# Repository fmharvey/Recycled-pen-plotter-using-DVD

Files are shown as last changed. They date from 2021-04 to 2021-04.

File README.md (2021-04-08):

# Recycled-pen-plotter-using-DVD
A recycled pen plotter using stepmotors from recycled DVD, a servo motor and a suite of hardware/softwares from the OpenSource community : Arduino, GRBL-Servo, UniversalGCodeSender ,  J Tech Photonics Inkscape Laser Plug-In , LinuxMint, EasyDriver pilot. What's my contribution - for now to have found all the bits to make it works as of 2021, an original design for the pencil holder/plater and some nice documentation in french/english as it is intented to be used as an activity in Quebec schools.

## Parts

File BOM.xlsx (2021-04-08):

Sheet: BOM
Composantes/kit
 |  | 8
Ref Schéma | Qte/1 | QteTot | Description | Provenance | Coût | Lien
 | 1 | 8 | Arduino UNO | magasin techno
 | 1 | 8 | Câble USB type B | magasin techno
 | 1 | 8 | ProtoBoard présoudé pour EasyDriver | magasin techno
 | 2 | 16 | EasyDriver | achat-financé C4
 | 1 | 8 | Alimentation externe 9V conn barrel 2.2mmID x 5.2 mm
 | 5 | 40 | Broches mâles cassables 0.1'' 2 pos
 | 1 | 8 | Broches mâles cassables 0.1'' 4 pos
 | 1 | 8 | Broches mâles cassables 0.1'' 3 pos
 | 10 | 80 | Brôche femelle 0.1'' 2 pos
 | 2 | 16 | Brôche femelle 0.1'' 4 pos
 | 2 | 16 | Brôche femelle 0.1'' 3 pos
 | 6 | 48 | Spacer Nylon 6mm haut X 6mm OD X 3.5mmID-pour stack easyr driver+arduino | magasin techno
 | 6 | 48 | Écrous 4/40 - pour stack EasyDriver+arduino | magasin techno
 | 6 | 48 | Vis nylon 4/40 -pour stack Easy Driver+arduino | magasin techno
 | 2 | 16 | Harnais 4 fils pour stepmoteur-Terminaison jumper mâle
 | 17 | 136 | Fil jumper mâle-mâle-easyr driver à arduino | magasin techno
 | 1 | 8 | Ordinateur récupéré | RécuperAction
 | 2 | 16 | Lecteur DVD | RécuperAction/C4
 | 2 | 16 | Boîtier lecteur DVD pré-troué (Seront troués après que les participants les auront démonté) | RécuperAction/C4
 | 2 | 16 | Équerres
 | 8 | 64 | Spacer imprimé 3D pour tenir les plateau | imprimé
 | 4 | 32 | Vis 1/4 -20 - pour les équerres
 | 4 | 32 | Écrous 1/4 -20 pour les équerres
 |  | 0
 | 4 | 32 | Ressorts compression plateau OD 7mm X ID 6mm X 20 mm long | magasin techno-récup
 | 4 | 32 | Vis M2.5 X20mm | Récupéré Axion
 | 4 | 32 | Écrou carré M2.5 | Récupéré Axion
 | 6 | 48 | TyRap réutilisable-pour tenir les plateaux
 | 2 | 16 | Plateau imprimé 3D - support tête | imprimé
 | 1 | 8 | Plateau à dessin | imprimé
 | 2 | 16 | Clips plateau à dessin
 | 1 | 8 | Plateau Servo-Crayon | imprimé
 | 1 | 8 | Ressort extension
 | 1 | 8 | Bague crayon imprimé 3D | imprimé
 | 2 | 16 | Vis M2.5 X 12mm pour bague crayon
 | 2 | 16 | Écrous carré M2.5 pour bague crayon
 | 1 | 8 | Servo moteur SG90
 | 1 | 8 | Harnais 3 fils pour Servo terminaison jumper mâle
Outils
 |  |  | Tapis antistatique
 |  |  | Fer à souder
 |  |  | Étain
 |  |  | Tournevis
 |  |  | Pince coupante
 |  |  | Pince à dégainer

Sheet: Logiciels
Logiciels
Logiciels | Version | Description | Hyperlien | Testé?
Arduino | 1.8.13 | On l'utilise seulement pour Uploader GRBL-Servo- ça pourrait être fait sans les étudiants | https://www.arduino.cc/en/software | Oui - Solution 1
GRBL-servo | plus récente | Pilote 'firmware' à installer sur la carte arduino- compatible avec plusieurs interface de contrôle - dont Universal G Code Sender . Basé sur la populaire librairie GRBL ave un tweak pour pouvoir contrôler un moteur servo à la place d'un troisième stepmoteur. | https://github.com/robottini/grbl-servo | Oui - Solution 1
Universal Gcode sender | plus récente | Application utilisant JAVA pour contrôler le traceur, calibrer les moteurs , modifier des paramètres de base et envoyer un fichier GCODE. | https://github.com/winder/Universal-G-Code-Sender | Oui - Solution 1
JAVA | V8 | Utilisé par le Universal Gcode Sender | https://www.java.com/fr/download/
Inkscape | V1.0 | Logiciel de dessin vectoriel OpenSource -Il faut installer une extension 'plugin' pour être capable de convetir une image vectoriel ou une image pixellisé en fichier GCODE . | https://inkscape.org/release/1.0/platforms/ | Oui - Solution 1
J Tech Laser Tool PLugin | Beta Version 1.0 | Extension à installer sur Inkscape pour convertir une image vectorisée en GCODE . L'application permet d'ajouter 2 commandes pour allumer/éteindre le laser qu'on peut remplacer par les commandes du servo.***C'est une extension en python - voire Stéphane pour voir si on peut changer les commandes LASER ON = M5 et LASER OFF= M3 S60 | https://jtechphotonics.com/?page_id=1980 | Oui - Solution 1
 |  | Voire ce logiciel - remplacerait Inkscape et le plugin : | https://github.com/inkcut/inkcut | à tester pour une solution 2
 |  | Voire ce site pour d'autres extensions Inkscape: | https://www.arnabkumardas.com/cnc.html | à tester pour une solution 2
FUSION 360-tinkercad |  | à déterminer -logiciel pour modifier les STL...

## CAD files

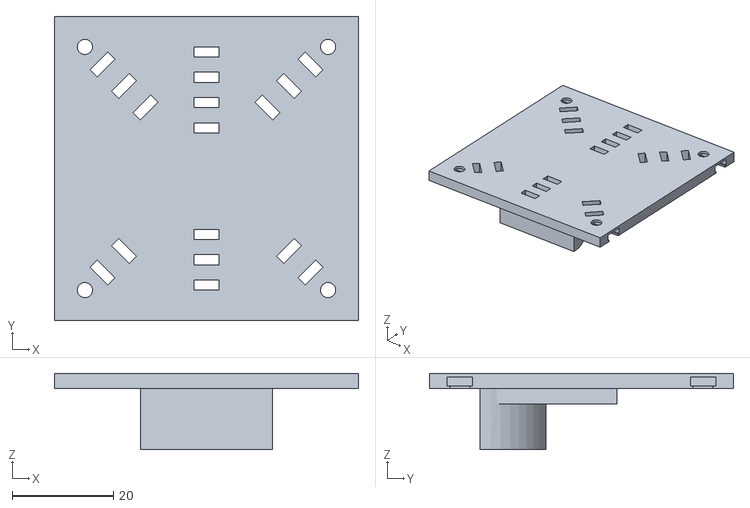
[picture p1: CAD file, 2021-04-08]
Attache-tete lecteur DVD.STL
60.0 x 60.0 x 15.0

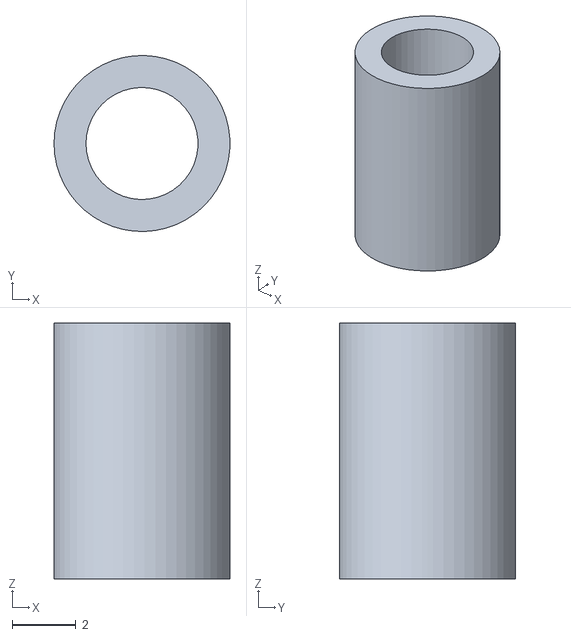
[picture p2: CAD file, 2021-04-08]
Entretoises EasyDriver.STL
5.50 x 5.50 x 8.00

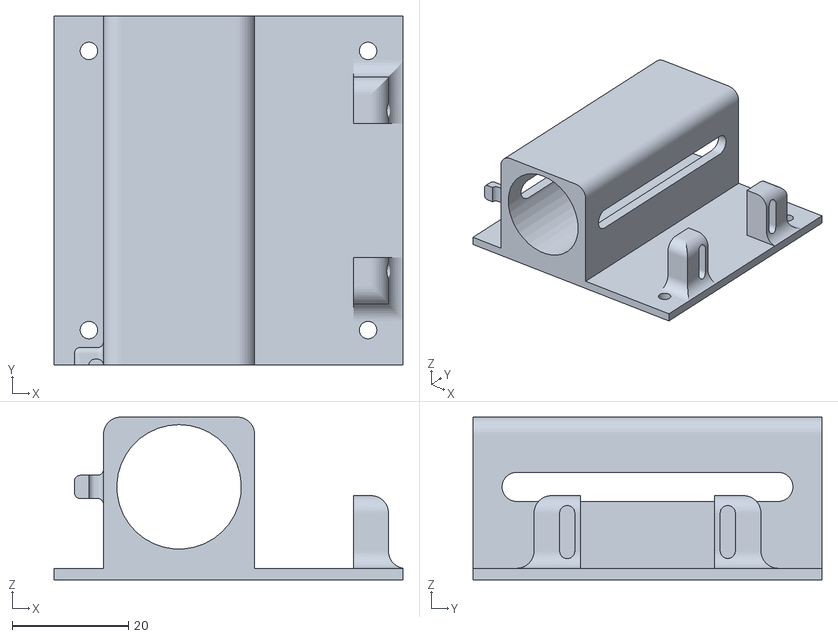
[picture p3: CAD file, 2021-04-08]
SupportServo-crayon.STL
60.0 x 60.0 x 28.0

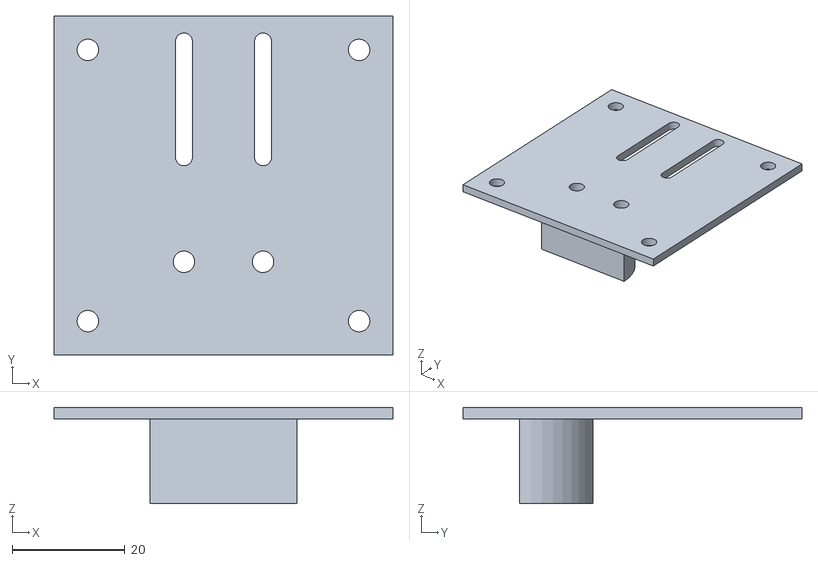
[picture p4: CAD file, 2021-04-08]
Plateau dessin.STL
60.0 x 60.0 x 17.0

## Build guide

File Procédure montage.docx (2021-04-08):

Feuille de route des activités pour la construction du mini traceur recyclé

# Introduction

Présentation des animateurs

Présentation du projet

Imprimante 3D en fonction

Traceur en fonction

OpenSource – logiciel et hardware

# A1 Extraction du lecteur DVD de l’ordinateur

Pousser pour enlever le panneau
Pousser pour lever le support du DVD. Débrancher les fils.
Appuyer sur le côté pour libérer le lecteur

# A2 Extraction des moteurs pas à pas et soudure des harnais

Matériel :

- Ordinateur avec lecteur DVD
- Lecteur DVD supplémentaire
- Crayon Sharpie ( pour identification des lecteurs)
- Câble de pratique à souder
- Poste de soudure (fer, étain, pince à dégainer, troisième main, tapis protecteur pour la table, lunette de sécurité, ventilateur aspirateur de fumée, gaine thermo rétractable, fusil chauffant)

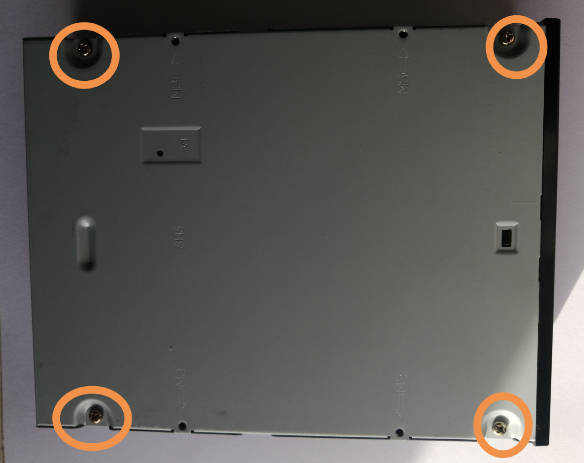
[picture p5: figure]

Enlever toutes les vis que vous voyez

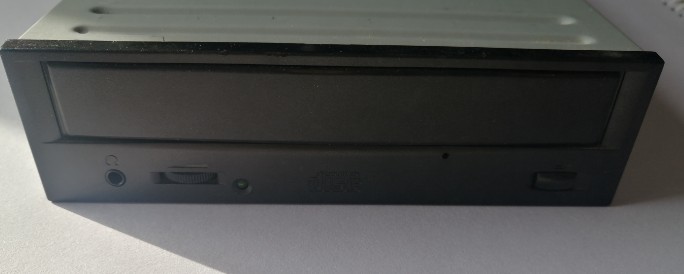
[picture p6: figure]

Localisez le petit trou à l’avant du lecteur, y insérer un trombone pour faire sortir le support à disque.

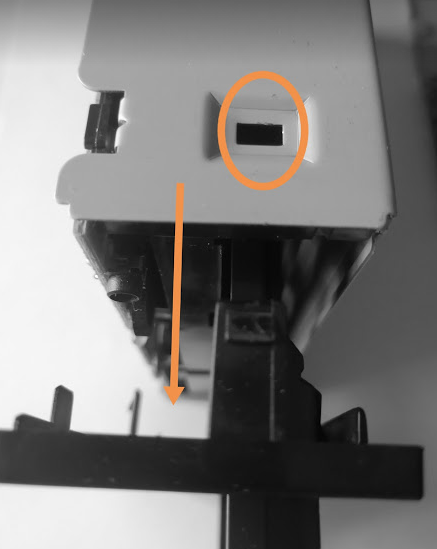
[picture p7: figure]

Appuyez sur les languettes pour les désengagez. Une fois qu’elles sont toutes désengagées tirer sur l’enceinte de plastique.
On peut maintenant ouvrir le boîtier métallique. On cherche le morceau dans la photo. Dévissez les vis, tirer sur les câbles plâts et retirer le moteur pas à pas. Identifiez le et remettez le | Photo des têtes lecteur DVD – mettre à garder/à mettre de côté

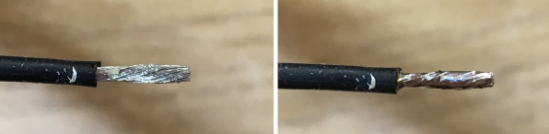
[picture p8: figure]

Soudure du harnais sur le moteur pas à pas. !Soudure de niveau expert sera fait pendant la semaine! À la place – soudure réparation de câble

# A3 Soudure des pilotes moteur

Matériel :

- Support visuel – vidéo d’une soudure
- Circuit de pratique à souder
- Carte ‘Protoshield’ modifié
- 2 Pilote moteur Easy Driver avec ensemble de connecteurs
- Vis et entretoise en plastique

Pratique de soudure de composante sur une carte
Souder Pilote moteur en X – Souder les brôches mâles en dessous – poser sur la carte Arduino pour s’assurer d’être droit.
Souder Pilote moteur en Y – Souder les brôches mâles sur le dessus.
Visser les deux pilotes ensemble.

# A4 Branchement des pilotes moteurs et présentation du Arduino

Matériel

- Pilote EasyDriver soudé
- Jumper femelle-mâle

| Photo vue du dessus et branchement
| Schéma de branchement complet pour les curieux

A5
